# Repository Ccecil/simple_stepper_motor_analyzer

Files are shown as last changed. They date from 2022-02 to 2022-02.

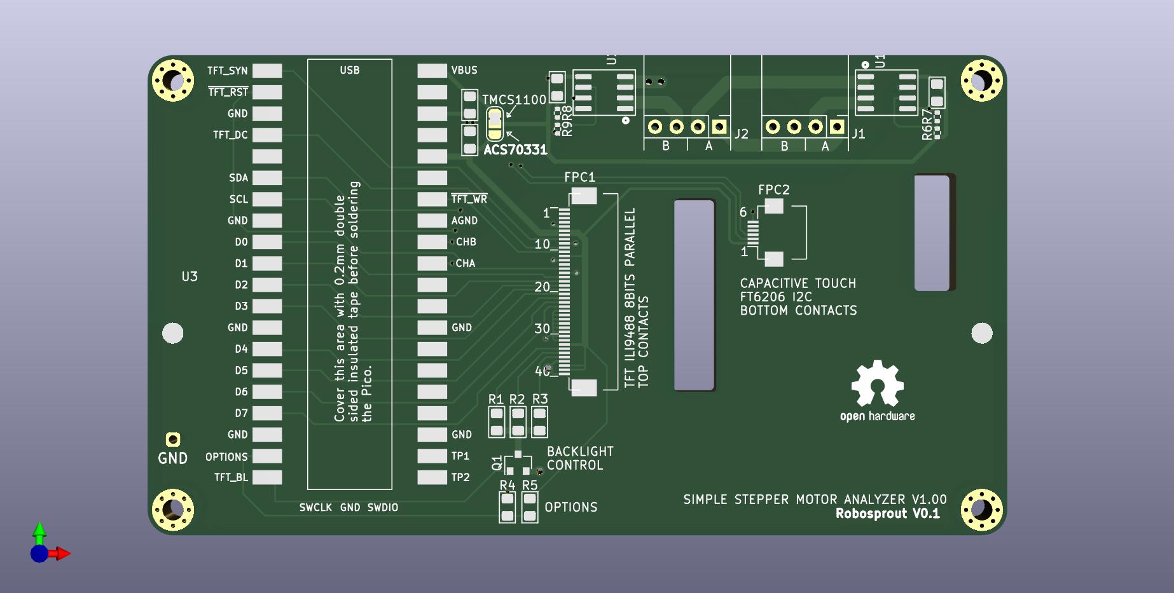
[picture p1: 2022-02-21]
kicad/stepper_analyzer_RSmod.jpg

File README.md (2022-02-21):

# Simple Stepper Motor Analyzer

Modifications made in this fork are largely due to parts shortages.  This allows the use of the TMCS1100A4-Q1 current sensor as an option.
Changes made:
&nbsp;
-Current sensor layout and traces
&nbsp;
-Added jumpers for switching 3.3/5v to the current sensors
&nbsp;
-Added voltage dividers to setup vref for the TMCS1100A4-Q1 (DNP if using default sensor)
&nbsp;
-Holes placed to orient the Stencil8 jig for ease of paste stenciling.
&nbsp;

<span style="color:red"><b>
NOTE (June 2021): The old design of the Simple Stepper Motor analyzer which was based on the STM32 was moved to https://github.com/zapta/legacy_stepper_motor_analyzer. This is a new and improve design that is based on the Raspberry Pi Pico and a 'bare' TFT panel.</b></span> 

&nbsp;

https://github.com/zapta/simple_stepper_motor_analyzer

&nbsp;



&nbsp;



&nbsp;

## Demonstration

Michael from the Teaching Tech youtube channel made [a great video explaining how stepper motors work](https://youtu.be/4iII25DGIdA) and used the Simple Stepper Motor Analyzer for some of the demonstrations. 



&nbsp;

## Highlights
* Low cost and minimalist DYI hardware design.
* Standalone. Doesn't require a computer to operate.
* Analyzes the stepper motor signals in the actual system (e.g. a 3D printer).
* Galvanically isolated current sensors. Does not interfere with the operating equipment, even when its turned off.
* Easy to connect using a pair 4 wire pass through connectors.
* Intuitive user interface with color display and a capacitive touch.
* Microstepping resolution of 1% of a full step.
* Provides momentary readings, signal patterns, and statistical measurements.
* Hardware and software are open sourced with a generous license.
* Based on free tools (Kicad, platformio, LVGL) and the Raspberry Pi Pico.
* Can be easily customized (new featured, cost reduction, data link to a computer, etc).
* Powered 5VDC, 200ma via a USB-C connector.

## Overview
Diagnosing the operation of stepper motor in 3D printers and CNC machines used to require stepper motor analyzers that costs thousands of dollar. Not anymore! The Simple Stepper Analyzer ('Analyzer' in short) brings these capabilities to every maker for a tiny fraction of the price and with a minimalist DIY electronic design that leaves the heavy lifting to the firmware.

The Analyzer is self contained, has two 4-wires pass-through connectors connecting the stepper motor, is powered from a common 5V charger with a micro USB cable, provides a simple to use graphical user interface with a 3.5" color touch screen, and provides a plethora of stepper motor measurements.

The Analyzer is provided to the community as a public domain reference design that can be built and used as is, or be customized with additional features or for a lower cost as desired. The hardware and firmware come with a liberal open source license (CC0) that allows commercial usages and doesn't require code source code sharing.

---
## Disclaimer
THE DESIGN IS PROVIDED "AS IS", WITHOUT WARRANTY OF ANY KIND, EXPRESS OR IMPLIED, INCLUDING BUT NOT LIMITED TO THE WARRANTIES OF MERCHANTABILITY, FITNESS FOR A PARTICULAR PURPOSE AND NONINFRINGEMENT. IN NO EVENT SHALL THE AUTHORS OR COPYRIGHT HOLDERS BE LIABLE FOR ANY CLAIM, DAMAGES OR OTHER LIABILITY, WHETHER IN AN ACTION OF CONTRACT, TORT OR OTHERWISE, ARISING FROM, OUT OF OR IN CONNECTION WITH THE DESIGN OR THE USE OR OTHER DEALINGS IN THE DESIGN.

---
## How does it work?
The principle of operation is very simple, and so is the hardware design. The stepper motor is connected via 4 wire pass-though connectors that allow the Analyzer to monitor the current through the stepper's coils. The Analyzer's user low impedance current sensors that are galvanically isolated such does not interfere with the operation of the 3D printer or other equipment it monitors. The Analyzer measures the coils currents 100k times a second and uses firmware that analyzes the data, extracts the desired measurements, and present them on the screen. For example, this is how an analysis of the distribution of distance by speed distribution looks like:



---
## Operation is simple and intuitive

1. Turn off power to the equipment (e.g. 3D printer).
2. Disconnect the 4 wires of the stepper motor and connect them through the Analyzer two pass through connectors.
3. Power the analyzer using a 5V charger and a micro USB cable.
4. Turn on the equipment and get the stepper going.
5. Use the Analyzer's screen to view the measurements you want.

**NOTE:** The two pass-through connectors of the Analyzer are symmetric and  each can act as an input or output. 

**CAUTION:** Always connect and disconnect stepper motors when their controller is not energized, to reduce the risk of damage to the controller due to high voltage spikes. The analyser itself is not subject to that risk since its uses galvanically isolated current sensors.



**NOTE:** The only requirement for proper wiring is that the two wires of one coil should go through pins pair 1,2 and the two wires of the other coil should go through pin pair 3,4. The Analyzer doesn't care about the +/- polarity of the wires in each pair, nor does it care which of the two pass-through connectors is on the controller side and which one is on the stepper side.

**TRIVIA:**: The pin-out and the connector type of the Analyzer follows the Duet3D conventions, except that is uses right angle connector to save space.

---
## The Home Page
The Home page is first page shown when the Analyzer is powered on. It provides summary information as well as access to the Settings page.



&nbsp;

#### Page Data

Field | Description
:------------ | :-------------
 COIL&nbsp;1 | Momentary coil 1 current in Amps.
 COIL&nbsp;2 | Momentary coil 2 current in Amps.
 ERRORS | The number of phase errors detected so far. Phase errors happens when the current patterns are so distorted that a forward/backward movement cannot be determined.
 POWER | Indicates if the stepper motor is currently energized. This is determined by the sum of currents in they two coils.
 IDLES | The number of times that stepper motor change status from energized to non energized.
 STEPS | The distance the stepper moved so far. Each full step forward increments this value by one and each full step backward decrements it by one. When the stepper motor is energized, the display also shows fractional steps in resolution of 1/100th of a full step.

HINT: The fractional step value cannot be reset because it is derived from the momentary currents in the two coils. Only the stepper motor driver can reset the fraction by positioning the stepper motor on an exact full step.

HINT: To swap forward/backward directions of the Analyzer use the Settings page. This does not affect the stepper motor itself.

&nbsp;
#### Page Actions

Action | Description
:------------: | :-------------
 | Clear all data.
 | Open the Settings page.

&nbsp;

---

## The Settings Page

This is a special page that is accessible from the Home page and allows to calibrate the Analyzer. The settings are stored in a non volatile memory and are preserved when the Analyzer is turned off.



&nbsp;
#### Page Data

Data | Description
:------------: | :-------------
COIL&nbsp;1 | The momentary current of stepper coil 1 in Amp units. Should be zero, or very close to zero, when the stepper motor is disconnected.
COIL&nbsp;2 | The momentary current of stepper coil 2 in Amp units. Should be zero, or very close to zero, when the stepper motor is disconnected.

&nbsp;
#### Page Actions

Action | Description
:------------: | :-------------
SET ZERO | Used to calibrate the zero reading of the current sensors. To do so, Disconnect the stepper motor and press this button.
REVERSE STEPS DIRECTION | Changes the forward/backward step directions of the Analyzer. Does not affect the stepper motor itself. Having the correct direction is important for measurements such as the Retraction analysis.
 | Press exist the Settings page.

&nbsp;

---

## The Speed Dial Page

This page measure the stepper speed in units of full steps per second. 



&nbsp;
#### Page Data

Data | Description
:------------ | :-------------
Speed&nbsp;Dial | The speed dial shows the momentary stepper speed in full steps per second units. Forward speed is on the right side and backward speed is on the left.
Speed&nbsp;Value | This field shows the speed in a numeric form. IT is updated less frequently than the dial to allow easy reading.

&nbsp;
**HINT:** The Settings page allows to swap the forward/backward directions.

&nbsp;
#### Page Actions

Action | Description
:------------: | :-------------
 | Clears all data.
Tap the dial |Toggles the dial's speed range.

&nbsp;

---

## The Distance Graph Page

This page shows scrolling graph with the total number of full steps vs. time.



&nbsp;

#### Page Data

Data | Description
:------------ | :-------------
Distance&nbsp;Graph | This graph shows how the distance, in units of full steps, changes over time.
Distance&nbsp;value | The numeric value of the distance in full steps.  This fields is identical to the STEPS field in the Home page.

&nbsp;

#### Page Actions

Action | Description
:------------: | :-------------
 | Clears all data.
Tap the graph | Toggles the range of the vertical axis.

&nbsp;

---

#### The Retraction Graph Page

This page is useful to analyze the retraction in of 3D printer extruder.



&nbsp;
**TRIVIA:** The graph above was taken while testing a direct extruder printer with [Thing #909901](https://www.thingiverse.com/thing:909901).
&nbsp;
#### Page Data

Data | Description
:------------ | :-------------
Retraction&nbsp;Graph | This graphs tracks the retraction of 3D extruder full step units.  Retraction is defined as the filament length that was inside the extruder and is now retracted outside of the extruder. 
Retraction value |  This field shows the current retraction level in a numeric form.

&nbsp;
#### Page Actions

Action | Description
:------------: | :-------------
 | Clear all data.
Tap the graph | Changes the range of the vertical axis.

&nbsp;

---

## The Time by Speed Page

This page shows an histogram with the distributing of time by stepper speed. That is how much time was spent in each speed range. The values are normalized such that the longest bar is always at 100%.



&nbsp;
#### Page Data

Data | Description
:------------ | :-------------
Time&nbsp;Histogram | The horizontal axis indicates speed in full steps per second units. The height of each bar indicate the time of all steps in that speed range, with the length of the longest bar normalized to 100%.

&nbsp;
#### Page Actions

Action | Description
:------------: | :-------------
 | Clear all data.

&nbsp;

---

## The Distance by Speed Page

This page shows an histogram with the the distribution of distance by stepper speed.



&nbsp;
#### Page Data

Data | Description
:------------ | :-------------
Distance&nbsp;Histogram |  The horizontal axis indicates speed in full steps per second units. The height of each bar indicate the distance or number of steps in that speed range, with the length of the longest bar normalized to 100%.

&nbsp;
#### Page Actions

Action | Description
:------------: | :-------------
 | Clear all data.

&nbsp;

---

## The Current by Speed Page

This page measures the ability of the stepper motor's controller to maintain peak current at high speeds.

The screenshot below shows a healthy system where the peak current is virtually flat across the speed range.



The screenshot below shows a system that is not capable to maintain peak current and starves the stepper motor at high speeds, resulting in poor torque and possible skipped steps.



&nbsp;
#### Page Data

Data | Description
:------------ | :-------------
Peak&nbsp;Current&nbsp;Histogram | The horizontal axis indicates speed in full steps per second units. The height of each bar indicates the average peak current in Amps of  steps that speed range. 

&nbsp;
#### Page Actions

Action | Description
:------------: | :-------------
 | Clear all data.

&nbsp;

---

## Coil Current Patterns Page

This page shows the current patterns in the two stepper coils.

The screenshot below shows a healthy system where the signals are nice and clean and reaches the target peak current.



&nbsp;

The screenshot below is from a poor system where high speed results in distorted and insufficient current, resulting in loss of torque and a potential for skipped steps.



&nbsp;

**GENERAL INFORMATION:** Each cycle of the stepper current pattern represent 4 full steps. The centers of those steps are at on the four vertical dotted lines where the currents of the two coils are identical, in the same or in  opposite polarities. The transitions between the steps are on the 4 vertical solid lines where one of the coils is at zero current. This cycle of 4 full steps is sometimes referred to as a single 'electric rotation'. The analyzer computes the exact phase on this cycle using the standard trigonometric function atan2(current1, current2) which can also be calculated manually from the current readings in the Home page.



&nbsp;

#### Page Data

Data | Description
:------------ | :-------------
Current&nbsp;graph | The horizontal axis indicates time in milliseconds. The vertical axis indicate coil current level in Amps. The two graphs show the current patterns of the respective stepper coils.

**NOTE:** The graph is updated only when sufficient stepper motor movement is detected.

&nbsp;
#### Page Actions

Action | Description
:------------: | :-------------
 | Clear all data.
 | When running, pauses the display updates.
 | When paused, resume the display updates.
Tap the graph | This toggles the range of the horizontal axis.

&nbsp;

---

## Coil Current Phase Page

This page draws the current patterns of the two coils as a [Lissajous curve](https://en.wikipedia.org/wiki/Lissajous_curve) which allows to examine visually distortions such as non sinusoidal current, phase distortion, and reduced amplitude.

In an ideal system, the graph is a perfect smooth circle, that doesn't change its size when the stepper's speed changes. Patterns that significantly diverge from that indicates a sub optimal configuration and operation.

Following picture shows a pattern from a well functioning system. The graph is round, reasonable smooth, and has sufficient size which indicates good current drive. 

The horizontal axis indicates the coil 1 current and the vertical axis indicates coil 2 current. In this example, both span nicely between -2A to +2A.



&nbsp;

The screenshot below is from a poor system where high speed results in distorted and insufficient current, resulting in loss of torque and a potential for skipped steps. The pattern is far from a clean circle and the shape has reduced size.



&nbsp;

The screenshot below shows a sub optimal operation where a a speed increase of the stepper results in small (less current and torque) and even more distorted curve.



&nbsp;

The screenshot below shows a well functioning system. The smaller size of the circle compare to the example above indicates that it operates on lower current.



&nbsp;

The screenshot below show an operation of a stepper in full steps mode. The dimension of the pattern indicate good current feed, and the square  shape is the best a full step driver can deliver.



&nbsp;

The screenshot below show an operation of a stepper in half steps mode. The dimension of the pattern indicate good current feed, and the shape is somewhere between the square shape of full step mode and the round shape of micro stepping interpolation mode.



&nbsp;

#### Page Data

Data | Description
:------------ | :-------------
Lissajous&nbsp;curve | A Lissajous curve drawn from the current pattern of coil 1 (x) and coil2(y). 
Capture speed | Shows the signal capture time. Fast mode works better with fast moving steppers and slow mode works with slow moving steppers. Tap the graph to toggle.

**NOTES** 
* The graph is updated only when sufficient stepper motor movement is detected.
* To view the current pattern that resulted in the current phase pattern, use the navigation button to switch the current patters page, and vice versa.

&nbsp;
#### Page Actions

Action | Description
:------------: | :-------------
 | Clear all data.
 | When running, pauses the display updates.
 | When paused, resume the display updates.
Tap the graph | This toggles the capture time between fast and slow speeds.

&nbsp;

---

## Reference Design Specification

Item | Specification
:------------ | :------------- 
Power consumption | 5V, 175ma.
Power connector | micro USB
MCU | Raspberry Pi RP2040 (Pico module).
Flashing | Drag and drop to a virtual disk.
Data link | USB/Serial link available but not used.
Current measurement | +/-2.5A per coil. (+/-5A sensors optional).
PCB | 102mm x 57mm, two layers
Enclosure | 3D printed, 108.4mm x 63.4mm x 16.6mm
Display | 3.5" 480 x 320, Color, Landscape mode.
Touch screen | Capacitive
Sensor isolation | See ACS70331 data sheet
Sampling rate | 100Khz per channel.
Sampling resolution | 12bits
Current accuracy | estimated at +/- 1%
Max step rate | Software dependent. Currently 2K full steps/sec.
Step resolution | 1/100th of a full step.
User settings storage | On board FLASH.
GUI framework | LVGL library. R3G3B2 color depth.
Programming language | C++
Programming IDE | VSCode, Platformio, WizIO.
Electronic design software | Kicad.
Mechanical design software | Onshape. 

&nbsp;

---

## I want to build me one

The electronic schematic, PCB layout, gerber files, and the firmware source files and released binary are all available on this github repository.

[Schematic](./kicad/stepper_analyzer.pdf)

[Production files](./kicad/JLCPCB)

[BOM](./kicad/BOM.xlsx)

&nbsp;

**Instructions:** Order the PCB with JLCPB with SMD service (see JLCPCB directory with gerbers and bom and pos files). Attach the Pico with XFasten tape and solder. Cut the bottom pins of the KF2510 connectors to 1mm length and solder from the top of the PCB only. Solder the current sensors, attach the TFT to the back of the PCB with XFasten tape and carefully connect the two FPC cables. Program the Pico by connecting it to a computer while it's bootsel button is pressed and drag he uf2 release file to the virtual disk you will see on your computer.

Note: The two servo connectors may be hard to insert and remove due to a small bump on the male side that is intended to lock in place the female connector. If you are handy with X-Acto knife, you can try carefully scraping that bump for easier insertion as I did (knives are sharp and may be dangarous, use proper precautions). 



&nbsp;



&nbsp;



&nbsp;



&nbsp;



## Mechanical
3D print the two part of the enclosure (STL files in this github repository), insert the four M2.5x3.5x3 heated inserts with a solder iron, drill the four  2.5 holes in the cover, insert the PCB to the front part, make sure the TFT seats flush with front and secure the back with four M2.5x10 hex cup screws.

## Ideas for improvements
The Analyzer is provided as a fully functional reference design and changes and the developers encourage improvement/modifications of the hardware and/or firmware are encouraged. This can include new features, new measurements and pages, extending the design to support 2 or 3 steppers at once to track the x/y/z of a 3D printer, reducing the hardware cost using less expensive screen TFT, or even eliminating the screen altogether and using the Analyzer as a dongle tethered to a computer via the existing USB/Serial link.

&nbsp;

---

## FAQ

#### Q: Can I buy from you a few units?

A: We cannot provide assembled units for the general public. For that reason, we released the design with CC Zero license with the hope that other entrepreneurs will do so.

#### Q: Where do you source the TFT panels?

A: We buy the '3.5 LCD CTP' variant here https://www.aliexpress.com/item/32862869103.html. The choice of TFT panel and the mechanical design of the PCB follows Dustin Watts' ESP32 Touchdown project https://www.tindie.com/products/dustinwattsnl/esp32-touchdown/ (with extra 2mm to the PCB's length for extra clearance for the threaded heat inserts).

#### Q: Can the firmware of the analyzer be updated?

A: Yes. New firmware is released as .uf2 files. To flash the analyzer with a compatible .uf2 follow the standard procedure of the Raspberry Pi Pico. Access to the BOTSEL button is provided by a hole at the back of the 3D printed enclosure.

#### Q: Why some footprints on the PCB are not populated?

A: The PCB design includes circuitry that helps developing firmware for the analyzer that is not necessary or helpful for normal opeation of the analyzer.

#### Q: Can the current scale of the two channels increased from +/-2.5A?

A: The PCB was designed to accept also +/-5A variants of the current sensors and the optionals resistors R8 R9 were added to allow configuring the firmware to know about the larger current scale. This however was not tried yet since most 3D printer steppers do not exceed currents of 2.5A.

#### Q: Why not a SPI based TFT?

A: We could not achieve fast enough display refresh rate with SPI so switched to 16 bit parallel data transfers. With the optimized firmware we can update rate equivalent to 200Mhz SPI. 

#### Q: Can a cheaper TFT/touch be used?
A: Yes, but it will require design changes.

#### Q: Can the TFT screen be eliminated?
A: Yes. The Analyzer has a USB/Serial output can a small Analyzer dongle can communicate with a computer program. This will require firmware changes.

#### Q: Can you add feature X or customization Y?

A: Most likely not. The reference design is provided for the community to change and mix.

#### Q: I want to commercialize or crowd source it, can you help me?

A: Not really. The reference design is open source and you will need to find others to help you. We don't mind though to answer questions.

#### Q: Where do I file a bug?

A: Use the github repository.

#### Q: Is it ok to connect/disconnect power to the Analyzer while my 3D printer prints?

A: Of course. The Analyzer is isolated from the stepper wires and should not interfere with the operation of the printer.

#### Q: The Analyzer uses LVGL lib, what is the license of that library?

A: At the time of writing this, the LVGL license is available here https://github.com/lvgl/lvgl/blob/master/LICENCE.txt.  The Analyzer's developers are not affiliated with LVGL.

#### Q: Is the LVGL library included in the Analyzer's repository?

A: It's not needed. LVGL is supported by platform.io so the Analyzer's project is set for platform.io to fetch LVGL automatically.

#### Q: Can the firmware be built with the standard Raspberry Pi Pico C++ SDK?

A: It should be but we didn't try it. Installing the SDK, libraries and tools using platformio and the WizIO Pico 'baremetal' distribution is easier.

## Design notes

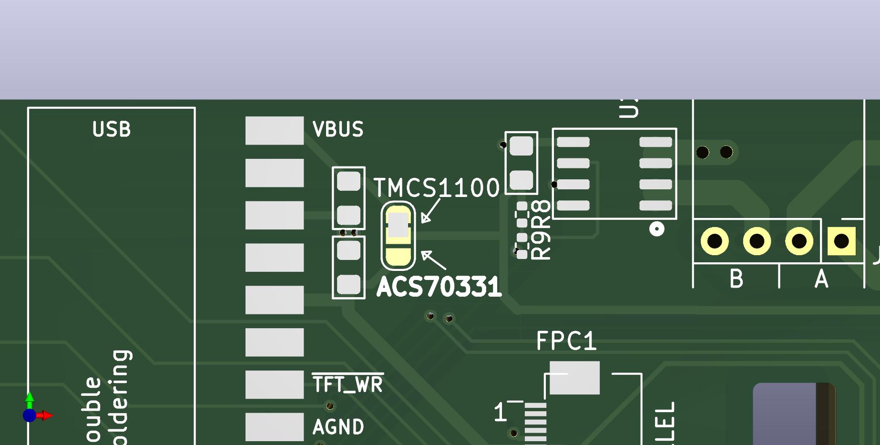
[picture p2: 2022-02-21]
kicad/jumper.jpg

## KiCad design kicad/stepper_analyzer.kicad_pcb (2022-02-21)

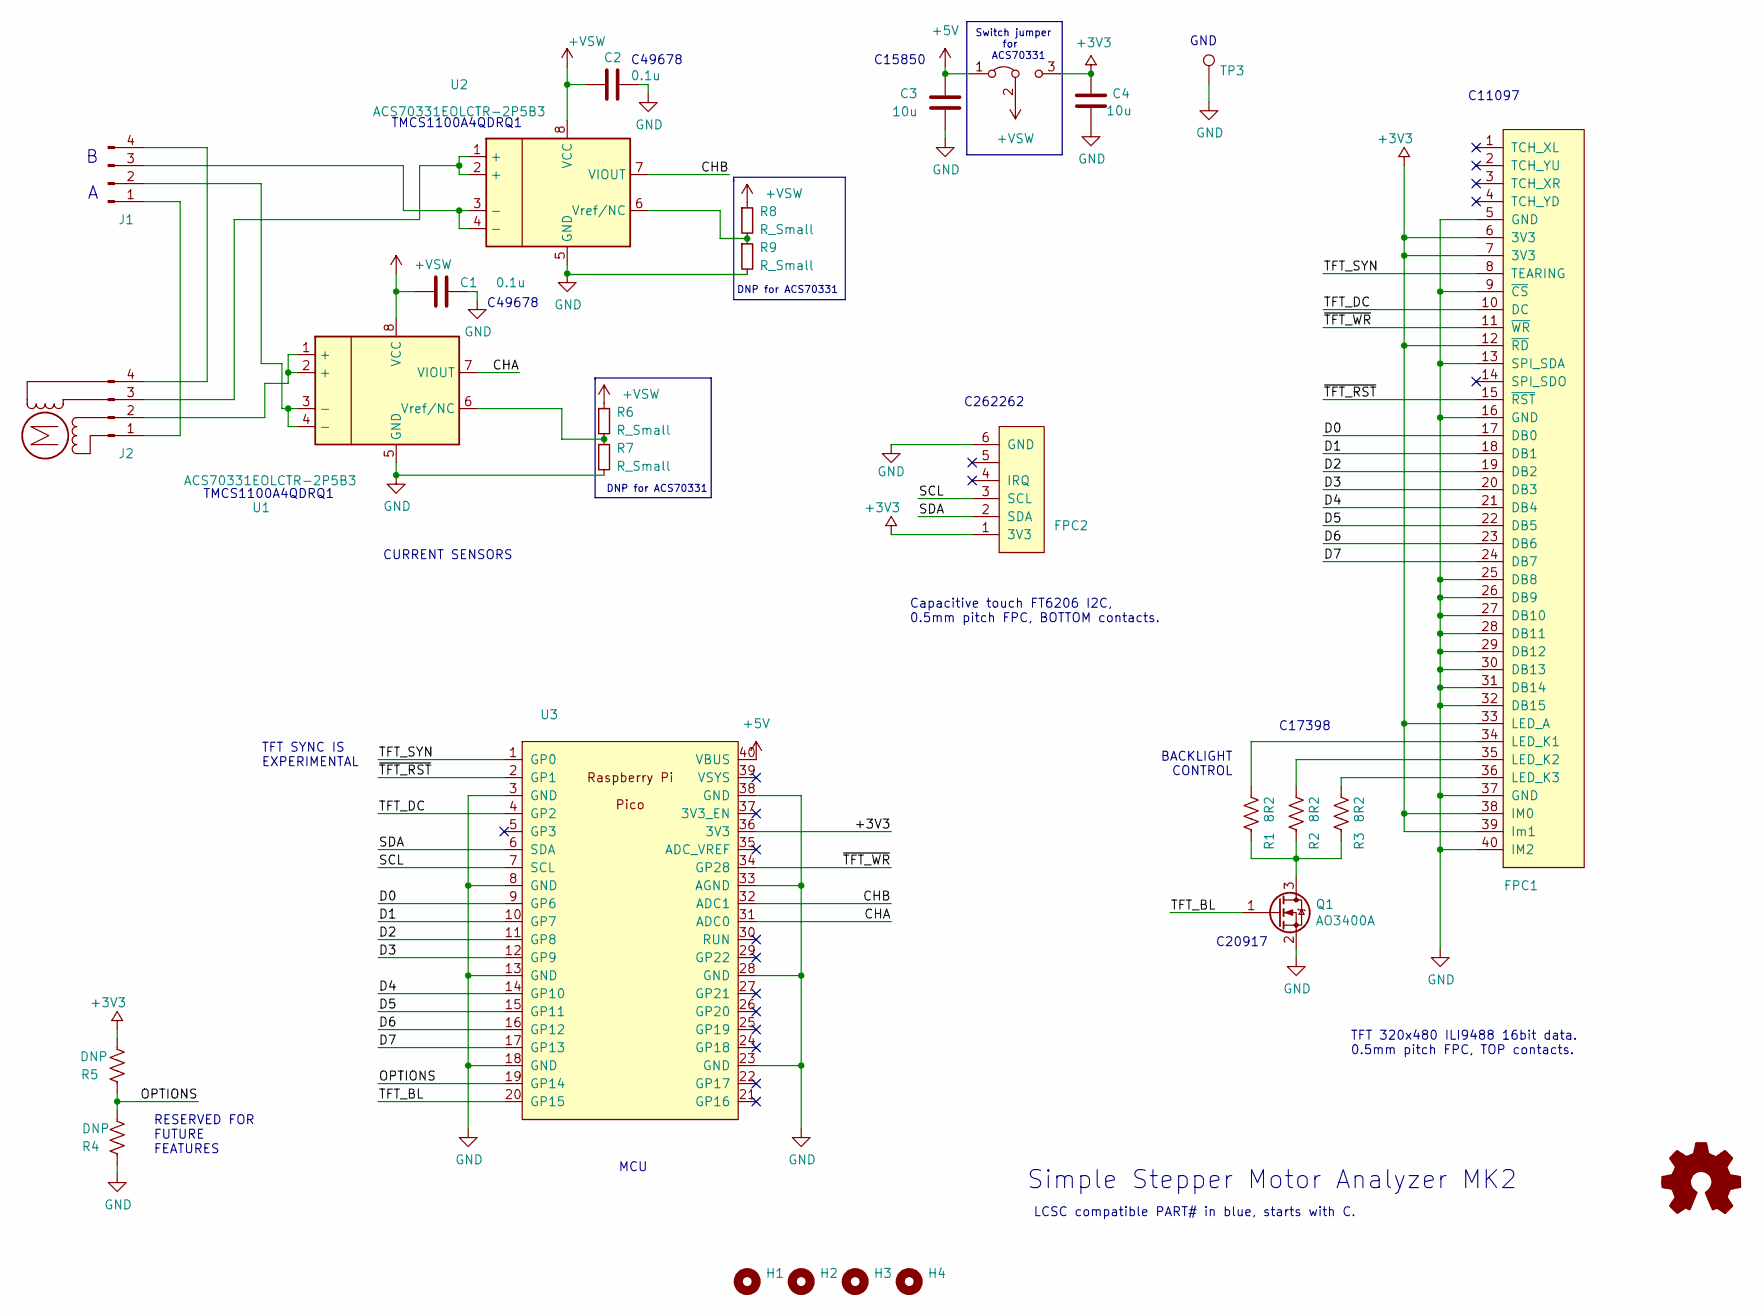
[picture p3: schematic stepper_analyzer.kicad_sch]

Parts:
C1, C2: 0.1u; C_0805_2012Metric_Pad1.15x1.40mm_HandSolder; LCSC C49678
C3, C4: 10u; C_0805_2012Metric_Pad1.15x1.40mm_HandSolder; LCSC C15850
FPC1: Connector_Conn_01x40_Female; JUSHUO-AFC07-S40ECC-00_40P_05mm_flipped; LCSC C11097
FPC2: FPC connector, 6 pins, 0.5mm, BOTTOM contacts; JUSHUO-AFC01-S06FCC-00_6p_05mm; LCSC C262262
H1, H2, H3, H4: MountingHole; MountingHole_2.5mm_Pad_Via
J1, J2: Connector_Conn_01x04_Male; connector_4pins_horizontal
JP1: Jumper_3_Bridged12; SolderJumper-3_P1.3mm_Open_RoundedPad1.0x1.5mm
LOGO1: Logo_Open_Hardware_Small; OSHW-Logo2_9.8x8mm_SilkScreen
M1: Motor; null_footprint
Q1: AO3400A; SOT-23; LCSC C20917
R1, R2, R3: 8R2; R_0805_2012Metric_Pad1.15x1.40mm_HandSolder; LCSC C25330
R4, R5: DNP; R_0805_2012Metric_Pad1.15x1.40mm_HandSolder_no_3d
R6, R7, R8, R9: R_Small; R_0402_1005Metric
TP3: TestPoint; testpoint_double_side
U1, U2: ACS70331EOLCTR-2P5B3; SOIC-8_3.9x4.9mm_P1.27mm
U3: Pico; Pico_smd_dedicated

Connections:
+3V3: C4.2, FPC1.6 (3V3), FPC1.7 (3V3), FPC1.12 (~RD), FPC1.33 (LED_A), FPC1.38 (IM0), FPC1.39 (Im1), FPC2.1 (3V3), JP1.3 (B), R5.2, U3.36 (3V3)
+5V: C3.2, JP1.1 (A), U3.40 (VBUS)
+VSW: C1.2, C2.2, JP1.2 (C), R6.1, R8.1, U1.8 (VCC), U2.8 (VCC)
/CHA: U1.7 (VIOUT), U3.31 (ADC0)
/CHB: U2.7 (VIOUT), U3.32 (ADC1)
/D0: FPC1.17 (DB0), U3.9 (GP6)
/D1: FPC1.18 (DB1), U3.10 (GP7)
/D2: FPC1.19 (DB2), U3.11 (GP8)
/D3: FPC1.20 (DB3), U3.12 (GP9)
/D4: FPC1.21 (DB4), U3.14 (GP10)
/D5: FPC1.22 (DB5), U3.15 (GP11)
/D6: FPC1.23 (DB6), U3.16 (GP12)
/D7: FPC1.24 (DB7), U3.17 (GP13)
/OPTIONS: R4.1, R5.1, U3.19 (GP14)
/SCL: FPC2.3 (SCL), U3.7 (SCL)
/SDA: FPC2.2 (SDA), U3.6 (SDA)
/TFT_BL: Q1.1 (G), U3.20 (GP15)
/TFT_DC: FPC1.10 (DC), U3.4 (GP2)
/TFT_SYN: FPC1.8 (TEARING), U3.1 (GP0)
/~TFT_RST: FPC1.15 (~RST), U3.2 (GP1)
/~TFT_WR: FPC1.11 (~WR), U3.34 (GP28)
GND: C1.1, C2.1, C3.1, C4.1, FPC1.5 (GND), FPC1.9 (~CS), FPC1.13 (SPI_SDA), FPC1.16 (GND), FPC1.25 (DB8), FPC1.26 (DB9), FPC1.27 (DB10), FPC1.28 (DB11), FPC1.29 (DB12), FPC1.30 (DB13), FPC1.31 (DB14), FPC1.32 (DB15), FPC1.37 (GND), FPC1.40 (IM2), FPC2.6 (GND), Q1.2 (S), R4.2, R7.2, R9.2, TP3.1, U1.5 (GND), U2.5 (GND), U3.3 (GND), U3.8 (GND), U3.13 (GND), U3.18 (GND), U3.23 (GND), U3.28 (GND), U3.33 (AGND), U3.38 (GND)
unnamed: FPC1.34 (LED_K1), R1.2
unnamed: FPC1.35 (LED_K2), R2.2
unnamed: FPC1.36 (LED_K3), R3.2
unnamed: J1.1, J2.1
unnamed: J1.2, U1.3 (-), U1.4 (-)
unnamed: J1.3, U2.3 (-), U2.4 (-)
unnamed: J1.4, J2.4
unnamed: J2.2, U1.1 (+), U1.2 (+)
unnamed: J2.3, U2.1 (+), U2.2 (+)
unnamed: Q1.3 (D), R1.1, R2.1, R3.1
unnamed: R8.2, R9.1, U2.6 (Vref/NC)
unnamed: R6.2, R7.1, U1.6 (Vref/NC)

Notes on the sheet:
CURRENT SENSORS
DNP for ACS70331
Switch jumper for ACS70331
TMCS1100A4QDRQ1
Simple Stepper Motor Analyzer MK2
TFT 320x480 ILI9488 16bit data. 0.5mm pitch FPC, TOP contacts.
RESERVED FOR FUTURE FEATURES
LCSC compatible PART# in blue, starts with C.
C17398
MCU
TFT SYNC IS EXPERIMENTAL
GND
Capacitive touch FT6206 I2C, 0.5mm pitch FPC, BOTTOM contacts.
C20917
C49678
C15850
C11097
C262262
BACKLIGHT CONTROL

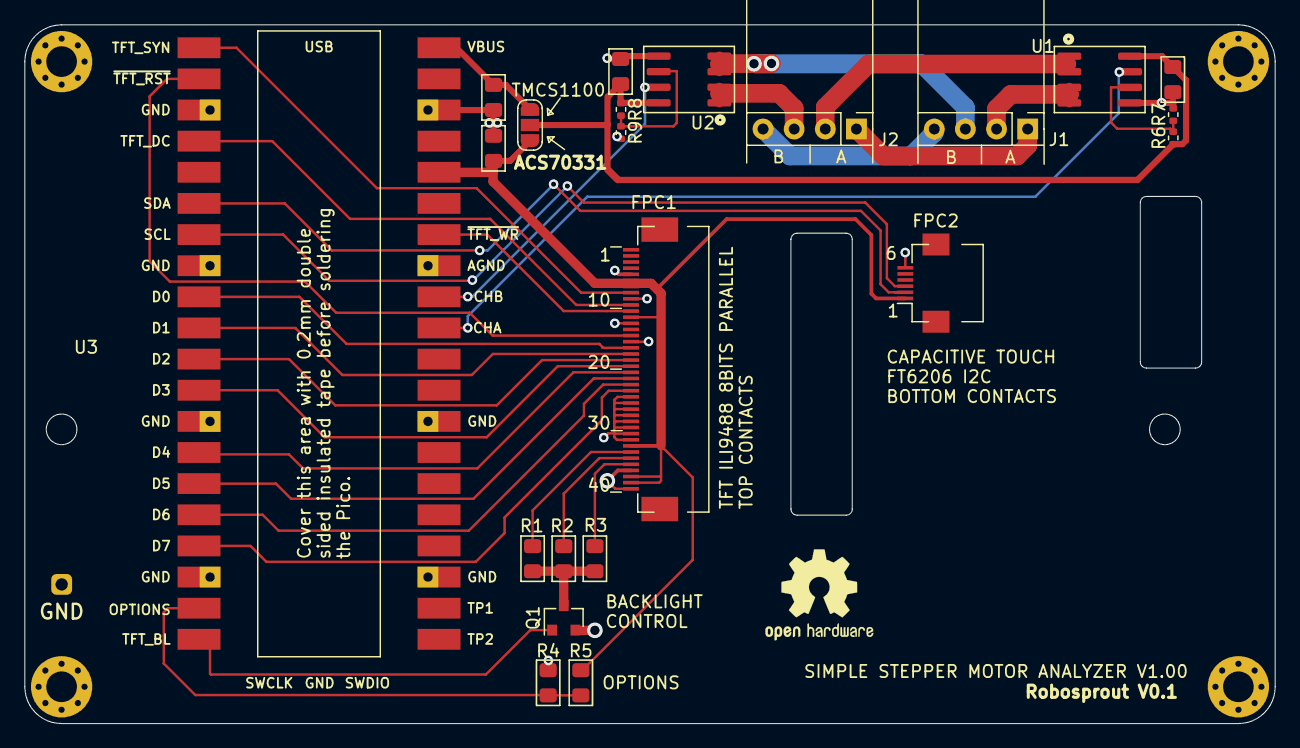
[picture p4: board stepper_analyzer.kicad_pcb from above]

Board: 2 copper layers, 102.0 x 57.0 mm, 29 parts (1 on the bottom side), 34 nets.
